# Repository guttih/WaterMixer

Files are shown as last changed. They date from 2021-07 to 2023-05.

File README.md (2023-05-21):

# Water Mixer

This project mixes water temperature from a 1/2" hot water pipe and a 1/2" cold water pipe out to a single 3/4" output 
water pipe.  A electrical valve controls the flow from the hot water pipe and another electrical valve controls the cold
water pipe.  A Temperature sensor is put into the 3/4" output water pipe to sense the current heat of the outgoing water.
Finally the third electrical valve is used to drain the hot tub. 

## Related links

- Project page (todo:)
- [Experiment page]
- [Hot-tub]
- Project [Development documents]

## Parts in project

- 1 x 12V Power supply
- 2 x [DC_STEPDOWN]
- 1 x [ESP32 Development Board]
- 1 x [DS18B20 Digital Temperature Sensor G3/4]
- 1 x [Logic level converter]
- 1 x [Dac MCP4728]
- 3 x [Proportional Valve Brass controllable with 0-5V]
- 1 x [LCD touch display]

## Api

Supported methods, requests and responses are described in the
[API methods]
## Wiring the project

### Schematic

```
                                                                                         +12V
                                                                                          ┬
  ┌───────────────────────────────────────────────────────────────────────────────────────┤
  │ ┌───────────────────┬──────────────────┬────────────────┬───────────────────────┬──┐  │
  │ │                   │                  │  ╔══════════╗  │  ╔═════════════╗      ┴  │  │
  │ │ ╔══════════════╗  │  ╔═════════════╗ │  ║ Pressure ║  │  ║     ADC     ║     GND │  │
  │ │ ║ POWER SOURCE ║  │  ║ DC_STEPDOWN ║ │  ║  Sensor  ║  │  ║   ADS1115   ║         │  │
  │ │ ║              ║  │  ║   -Vo(GND) -╟─┘  ║          ║  │  ║             ║         │  │
  │ │ ║              ║  │  ║   +Vo(+5V) -╟─┐  ║    Black-╟──┴──╢-G           ║         │  │
  │ │ ║              ║  │  ║             ║ │  ║    Green-╟─────╢-A0          ║         │  │
  │ └─╢-     GND    -╟──┴──╢-GND         ║ │  ║          ║     ╢-A1          ║         │  │
  └───╢-    +12V    -╟─────╢-VIN         ║ │  ║          ║     ╢-A2          ║         │  │
      ╚══════════════╝     ╚═════════════╝ │  ║          ║     ╢-A3          ║         │  │
                                           │  ║      Red-╟─┬───╢-V           ║         │  │
                      +5V                  │  ╚══════════╝ │ ┌─╢-CL       DA-╟─┐       │  │
                       ┬  ┌────────────────┴───────────────┘ │ ╚═════════════╝ │       │  │
                       └──┤                                  │                 │       │  │
                          │ ╔═══════════╗                    │ ╔═════════════╗ │       │  │
                          │ ║  -ESP32-  ║  ╔═════════════╗   │ ║     DAC     ║ │       │  │
                          │ ║           ║  ║ Logic Level ║   │ ║   MCP4728   ║ │       │  │
                          │ ║           ║  ║  converter  ║   │ ║             ║ │       │  │
                          └─╢-VIN   G14-╟──╢-LV3     HV3-╟───┴─╢-CL          ║ │       │  │
                            ║       G13-╟──╢-LV4     HV4-╟─────╢-DA───────DA-╟─┘       │  │
 +3V3   ╔═══════════╗       ║           ║  ║             ║     ║             ║         │  │
  ┬     ║  Resistor ║       ║           ║  ║             ║ +5V ║           D-╟──────┐  │  │
┌─┴─────╢-  4.7kΩ  -╟─────┬─╢-G25       ║  ║             ║  ┬  ║           C-╟      │  │  │
│       ╚═══════════╝     │ ║       3V3-╟──╢-LV       HV-╟──┴──╢-V         B-╟────┐ │  │  │
│       ╔═══════════╗     │ ║       GND-╟──╢-GND     GND-╟──┬──╢-G         A-╟──┐ │ │  │  │
│       ║  DS18B20  ║     │ ║           ║  ╚═════════════╝  ┴  ╚═════════════╝  │ │ │  │  │
│       ║   Temp    ║     │ ║           ║                  GND                  │ │ │  │  │
│       ║           ║     │ ║           ║                                       │ │ │  │  │
│       ║    SIGNAL-╟─(YE)┘ ║           ║   ┌───────────────────────────────────┘ │ │  │  │
├──(RD)─╢-VCC       ║       ║           ║   │    ┌────────────────────────────────┘ │  │  │
│ ┌(BL)─╢-GND       ║       ║           ║   │    │    ┌─────────────────────────────┘  │  │
│ │     ╚═══════════╝       ║  -ESP32-  ║   │    │    │        ╔════════════╗          │  │
│ │                         ║           ║   │    │    │        ║   Valve D  ║          │  │
│ │                         ║           ║   │    │    │        ║        GND-╟─(BL)─────┤  │
│ │                         ║           ║   │    │    └───(GR)─╢-LIN    ERR-╟─(YE)─    ┴  │
│ │                         ║           ║   │    │             ║    PWM Out-╟─(WT)─   GND │
│ ├─────────────────────┬───╢-GND       ║   │    │             ║        VCC-╟─(RD)────────┤
│ │  ╔══════════════╗   │   ║           ║   │    │             ╚════════════╝             │
│ │  ║   LCD TOUCH  ║   │   ║           ║   │    │             ╔════════════╗             │
│ │  ║    DISPLAY   ║   │   ║           ║   │    │             ║   Valve C  ║             │
│ │  ║              ║   │   ║           ║   │    │             ║        GND-╟─(BL)─────┐  │
│ │  ║          GND-╟───┘   ║  -ESP32-  ║   │    └─────── (GR)─╢-LIN    ERR-╟─(YE)─    ┴  │
│ │  ║      SD_MOSI-╟─┐     ║           ║   │                  ║    PWM Out-╟─(WT)─   GND │
│ │  ║         MOSI-╟─┼───┐ ║           ║   │                  ║        VCC-╟─(RD)────────┤
│ │  ║        T_DIN-╟─┘   │ ║           ║   │                  ╚════════════╝             │
│ │  ║       SD_SCK-╟─┐   │ ║           ║   │                  ╔════════════╗             │
│ │  ║          SCK-╟─┼─┐ │ ║           ║   │                  ║   Valve H  ║             │
│ │  ║        T_CLK-╟─┘ │ └─╢-G23       ║   │                  ║        GND-╟─(BL)─────┐  │
│ │  ║         T_DO-╟─┐ └───╢-G18       ║   └─────────────(GR)─╢-LIN    ERR-╟─(YE)─    ┴  │
│ │  ║      SD_MISO-╟─┴─────╢-G19       ║                      ║    PWM Out-╟─(WT)─   GND │
│ │  ║           CS-╟───────╢-G15       ║                      ║        VCC-╟─(RD)────────┤
│ │  ║        RESET-╟───────╢-G4        ║                      ╚════════════╝             │
│ │  ║           DC-╟───────╢-G2        ║  ┌─────────────────────────┐                    │
│ │  ║        SD_CS-╟───────╢-G5        ║  │        ╔═════════════╗  │                    │
│ │  ║         T_CS-╟───────╢-G21       ║  │        ║ DC_STEPDOWN ║  │                    │
│ │  ║              ║       ║  -ESP32-  ║  │        ║             ║  │                    │
│ │  ║          VCC-╟─┐     ╚═══════════╝  │  ┌─────╢- -Vo( GND) -╟  │  ┌────┐            │
│ │  ║          LED-╟─┴────────────────────┘  │  ┌──╢- +Vo(+3V3) -╟──┘  │    ┴            │
│ │  ╚══════════════╝                         │  │  ║         GND-╟─────┘   GND           │
│ └───────────────────────────────────────────┘  │  ║         VIN-╟───────────────────────┘
└────────────────────────────────────────────────┘  ╚═════════════╝                         
```
Legend

- <span style="background: black; color: white">(BL) = Black wire (-Ground)</span>
- <span style="background: red; color: white">(RD) = Red wire (+VCC)</span>
- <span style="background: yellow; color: black">(YE) = Yellow wire</span>
- <span style="background: green; color: white">(GR) = Green wire (voltage signal)</span>
- <span style="background: white; color: black">(WT) = White wire</span>
- GND    : Ground.
- ` ┴` 
- `GND`  : Ground.  When there is no room to connect the GND on the drawing, this notation is used.  Note, *all grounds are connected together*.
- VIN    : 5V pin on the esp32 pin.
- G34    : Esp32 GPIO 34 pin which is used to measure voltage coming from pressure sensor.
- G25    : Esp32 GPIO 25 pin which is used to communicate with the temperature sensor.
- G12    : Esp32 GPIO 12 pin which is used control the hot water valve.
- G14    : Esp32 GPIO 14 pin which is used control the cold water valve.
- G32    : Esp32 GPIO 32 pin which is used control the drain water valve.
- G##    : Other esp32 pins used to control the touch display and read and write to a sd card.
- Valve H: Hot valve
- Valve C: Cold valve
- Valve D: Drain valve

## Software development

The software for this project was developed using [PlatformIO].

### Tests

There are two kinds of tests in this project, *integration tests* and *unit tests*.

__Integration tests__:
*integration tests* are located in the `./test` directory.

On windows 10, best would be if you would add this location to your PATH system environment variable __C:\Users\your_user_name\.platformio\penv\Scripts__ to get access to the pio.exe application.
C:\Users\gudjons\.platformio\penv\Scripts
Then you can run the tests with this command `pio test`

[DC_STEPDOWN]:https://www.aliexpress.com/item/32531438467.html?spm=a2g0s.9042311.0.0.27424c4dWJSXmG
[ESP32 Development Board]:https://www.aliexpress.com/item/32801621054.html?spm=a2g0s.9042311.0.0.27424c4dOggB1n
[DS18B20 Digital Temperature Sensor G3/4]:https://www.aliexpress.com/item/32881183992.html?spm=a2g0s.12269583.0.0.43c751fcxDyDbt
[Logic level converter]:https://www.aliexpress.com/item/32308653416.html?spm=a2g0s.9042311.0.0.27424c4dy510IB
[Dac MCP4728]:https://www.aliexpress.com/item/32975252305.html?spm=a2g0s.12269583.0.0.142b3d73bl1KXq
[Proportional Valve Brass controllable with 0-5V]:https://www.aliexpress.com/item/33037988030.html?spm=a2g0s.12269583.0.0.49d04a42eL9zNl
[Experiment page]: https://guttih.com/list/project-hottub-temp
[Hot-tub]:http://192.168.1.79/list/project-hottub
[cmake]:https://cmake.org/download/#latest
[PlatformIO]:https://platformio.org/
[Development documents]: docs/development/development.md
[LCD touch display]: https://www.aliexpress.com/item/4000030399357.html?spm=a2g0s.12269583.0.0.687d6973QvjfAl
[API methods]: docs/apiMethods.adoc

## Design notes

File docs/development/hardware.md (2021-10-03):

# Hardware
This document describes each device, what voltage it uses and where it was bought.

## esp32
__Esp32 Development board__

This device handles all the work and is connected to all other devices.

 - Bought [here](https://www.aliexpress.com/item/32801621054.html?spm=a2g0s.9042311.0.0.27424c4dOggB1n)
 - Inventory [Here](http://parts.guttih.com/parts/view/5bfab5e0ec065a5ac2786934)

## temperature_sensor
__DS18B20 3/4" temperature sensor__ 

The sensor provides information on the water pressure in the pipe connected to the hot tub.  
It can run on both 5V and 3.3V power.

- Bought [DS18B20 Color L30mm Thread Specification 3/4"](https://www.aliexpress.com/item/32881183992.html?spm=a2g0s.12269583.0.0.43c751fcxDyDbt) 
- Inventory [Here](http://parts.guttih.com/parts/view/60c1c1c063ec3e056918c551)

## LLC 
__Logic level converter__

This device is used to convert 3.3V logic signals from the esp32 to 5V logic signals for the DAC.

- Bought [here](https://www.aliexpress.com/item/Free-shipping-4-channel-IIC-I2C-Logic-Level-Converter-Bi-Directional-Module-5V-to-3-3V/32308653416.html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)
- Inventory [Here](http://parts.guttih.com/parts/view/5bf9e9d1a66f3c7ee749efc5)

## MCP4728 
__DAC MCP4728 Module__

This device is used to send voltage ranging from 0-5 volts which a proportional
valve understands.

- Bought [here](https://www.aliexpress.com/item/32975252305.html?spm=a2g0s.12269583.0.0.142b3d73bl1KXq)
- Inventory [Here](http://parts.guttih.com/parts/view/61110ca1643bf7053b856df2)

## proportional_valve
__12V Proportional Valve__

There are three valves in this project, one 3/8" and two 3/4" valves.  They work exactly the same so we will consider 
them all three units of the same device.  The 3/8" unit will be controlling the drain water flow.

- Bought 2 x [Voltage: DC9V to DC24V, Specification: DN20 BSP Thread, Wiring Control: 0V to 5V Signal](https://www.aliexpress.com/item/32819881011.html?spm=a2g0s.12269583.0.0.112c1eaeyGDt8f)
- Bought 1 x [Voltage:DC9V-24V 0-5V, Specification: DN10 Brass Valve, Thread Type: NPT](https://www.aliexpress.com/item/33037988030.html?spm=a2g0s.12269583.0.0.6c674a42N25diC)
- Inventory [Here](http://parts.guttih.com/parts/view/5e2589736d7d870510d99be2)

## lcd_touch_display
  __3.2 Display module with touch and SD card reader__

  The device __needs 3.3V__ power to work.  The J1 has been soldered so 5V is out of the question.

- Bought [here](https://www.aliexpress.com/item/33040270372.html?spm=a2g0s.12269583.0.0.437c3e40dV19J4)
- Inventory [Here](http://parts.guttih.com/parts/view/60f1a0d4ea0ad5055e96116e)

## 12v_power_supply

Needed to power the three _12V Proportional Valves_

__Not selected yet__
- Bought todo: select product
- Inventory todo: add product to inventory

## 5v_power_supply

__DC_STEPDOWN__ 

This small adjustable step down power supply is needed to supply the pressure sensor and the Esp32 with power.
This unit will get power from the __12v_power_supply__ and will be be adjusted to give __5.05V__ output power.

- Bought [DC_STEPDOWN](https://www.aliexpress.com/item/32531438467.html?spm=a2g0s.9042311.0.0.27424c4dWJSXmG)
- Inventory [Here](http://192.168.1.79:6300/parts/view/5bfae6c1ec065a5ac278698f)

## 3v3_power_supply

__DC_STEPDOWN__ 

This small adjustable step down power supply is needed to supply the temperature sensor and the lcd touch display with power.
This unit will get power from the __12v_power_supply__ and will be be adjusted to give __3.2V__ output power.

- Bought [DC_STEPDOWN](https://www.aliexpress.com/item/32531438467.html?spm=a2g0s.9042311.0.0.27424c4dWJSXmG)
- Inventory [Here](http://192.168.1.79:6300/parts/view/5bfae6c1ec065a5ac278698f)

## pressure_sensor

This sensor needs 5V power to work and provides information on the water pressure in the pipe connected to the hot tub.

- Bought ~~[Pressure Sensor 5V 1/8" 5 Psi](https://www.aliexpress.com/item/4000263209249.html?spm=a2g0s.12269583.0.0.5dd91d80iwCJ6y)~~ which is incorrect because it woks on 0-0.345 bars
- Should have bought [Pressure Sensor 5V 1/8" 60 Psi](https://www.aliexpress.com/item/4000263209249.html?spm=a2g0s.12269583.0.0.5dd91d80iwCJ6y) which works on 0-4 bars.
- Inventory [Here](http://parts.guttih.com/parts/view/60cc6e7b395390058cb396d8)

 ### Related pages
 * [Readme]
 * [Product requirements]
 * [System requirements]
 * [Product requirements]
 * [User stories]
 * [Hardware]
 * [Releases]

[Readme]: ../../README.md
[Product requirements]: ./productRequirements.md
[System requirements]: ./systemRequirements.md
[User stories]: ./userStories.md
[Hardware]: ./hardware.md
[Releases]: ./releases.md

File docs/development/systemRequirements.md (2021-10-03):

# System Requirements
This document (SRD) provides information about what environment and hardware will be needed to make this product work.

## Hardware requirements

In general to make this product work these hardware modules will be needed.

Table column description:
  * __Hardware Id__ A short, unique, one word name of the hardware or device in question.
  * __Name__ Name of the part.
  * __Units__ How many peases of this kind of part is needed.
  * __R__ For what release is this parted needed.  Read about [Releases].

|  Hardware Id | Name | Units | R | The device is needed because |
|:---:|---|:---:|---|---|
| [esp32] | ESP32 Development Board | 1 | [0.5] | Control everything |
| [temperature_sensor] | DS18B20 3/4" temperature sensor | 2 | [0.5] | Provide water temperature in the outgoing pipe |
| [LLC] | Logic level converter - 4 channels | 1 | [0.5] | To allow esp32 to control DAC on 5V |
| [MCP4728] | Digital to analog converter (DAC) | 1 | [0.5] | Allow esp32 to control the valves |
| [proportional_valve] | Proportional Valve Brass controllable with 0-5V | 3 | [0.5] | To control the water flow in the pipes |
| [lcd_touch_display]  | 2.8" LCD Touch Display | 1 | [0.5] | To pass user information and get input from user |
| [12v_power_supply] | 12 volt power supply | 1 | [0.5] | Power the three [proportional_valve] |
| [5v_power_supply] | 5 volt power supply | 1 | [0.5] | Power [esp32], [temperature_sensor] and [pressure_sensor] |
| [3v3_power_supply] | 3.3 volt power supply | 1 | [0.5] | Power [lcd_touch_display] |
| [pressure_sensor] | 60 psi pressure sensor | 1 | [0.5] | Needed to test the water level of the hot tub |

## The Plumbing

This diagram shows the general idea, on where the electric valves and sensors should be located in the water pipe system.
Overview image of the whole system

 ### Related pages
 * [Readme]
 * [Product requirements]
 * [System requirements]
 * [Product requirements]
 * [User stories]
 * [Hardware]
 * [Releases]

[Readme]: ../../README.md
[Product requirements]: ./productRequirements.md
[System requirements]: ./systemRequirements.md
[User stories]: ./userStories.md
[Hardware]: ./hardware.md
[Releases]: ./releases.md

[0.5]: ./releases.md#release-05---bare-minimum
[0.6]: ./releases.md#release-06--hardware-installed
[0.7]: ./releases.md#release-07---additional-features
[0.8]: ./releases.md#release-08---remote-access
[0.9]: ./releases.md#release-09---boxed
[1.0]: ./releases.md#release-10
[1.1]: ./releases.md#release-11

[esp32]: ./hardware.md#esp32
[temperature_sensor]: ./hardware.md#temperature_sensor
[LLC]: ./hardware.md#LLC
[MCP4728]: ./hardware.md#MCP4728
[proportional_valve]: ./hardware.md#proportional_valve
[lcd_touch_display]: ./hardware.md#lcd_touch_display
[12v_power_supply]: ./hardware.md#12v_power_supply
[5v_power_supply]: ./hardware.md#5v_power_supply
[3v3_power_supply]: ./hardware.md#3v3_power_supply
[pressure_sensor]: ./hardware.md#pressure_sensor

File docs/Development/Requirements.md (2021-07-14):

# Product requirements
This Product Requirements Document(PRD) describes the requirements the Water mixer project needs to fulfill.  In this 
document, the Water mixer project and all its components will be referred to as the unit.

## Purpose
The main purpose of this project is to provide a user with an easy way to control water flow to and from a hot tub.  
A user should be able to command the unit to fill a hot tub at a specific temperature.  The user should be able to use 
it to control how fast the water flows to the hot tub and also to drain the hot tub.

To achieve this the unit will need to provide the user with information about it’s status and a way to give it commands.
  The user should be able to get the status and and give commands in two ways:

  * __At premises__ When the user is standing in front of the device he should be able to see it’s status, that is, 
  view the value of any status variable and to be able to give any of the available commands.

  * __Remotely__   When the user is not standing in front of the unit, he should be able to see it’s status, that is, 
  view the value of any status variable and to be able to give any of the available commands.

## Features
To be able to fulfill the purpose of this product the features will need to be described and implemented before release.  
They need to be prioritized and later selected into releases.  High priority features will be released first, 
and other lower priority features will be selected and released later.

### Users
Description of the two main personas this product is intended for.
 
   * __John__ is a 30 years old DIY kind a guy.  John knows a little programming, knows about GitHub and knows 
   JavaScript.  He understands the concept of a API and what a PID controller does, but is no specialist.

   * __Kamila__ is a non 11 years old non technical kind a girl.  She knows how to use a computer and a phone and 
   knows how to use a web browser.

Table column description:
  * __Feature Id__ Short one word name of feature
  * __User Story__ As a [persona], I [want to], [so that]
  * __P__ Priority/Importance of the feature. Available values: `H` `N` `L`. Where H=High, N=Normal and L = Low.
  * __R__ Feature is selected into a release numbered something. Read about [Releases].
  * __Notes__ Additional considerations or better explanation of the story.

|  Feature Id | User Story | P | R | Notes |
|:---:|---|---|---|---|
| LCD_FILL | As Kamila, I stand in front of the unit and want to fill the hot tub | H | [0.5] | |
| LCD_STOP | As Kamila, I stand in front of the unit and want to stop the flow to the hot tub | H | [0.5] | |
| LCD_DRAIN | As Kamila, I stand in front of the unit and want to drain the hot tub | H | [0.5] | |
| LCD_STATUS_TEMP | As Kamila, I stand in front of the unit and want to know the water temperature | N | [0.5] | |
| LCD_TEMP | As Kamila, I stand in front of the unit and want to change the water temperature flowing to the hot tub | H | [0.5] | |
| LCD_STATUS_FLOW | As Kamila, I stand in front of the unit and want to know the water flow rate | N | [0.7] | |
| LCD_FLOW_SLOW | As Kamila, I stand in front of the unit and want to make water flow slowly to the hot tub | N | [0.7] | |
| LCD_STATUS_WHEN_FULL | As Kamila, I stand in front of the unit and want to know when the hot tub will be full | L | [1.0] |  This is after some one has initiated the fylling process |
| LCD_STATUS_WHEN_EMPTY  | As Kamila, I stand in front of the unit and want to know when the hot tub will be fully drained | L | [1.0] |  This is after some one has initiated the draining process |
| LCD_STATUS_WATER_LEVEL | As Kamila, I stand in front of the unit and want to know the current hot tub water level | L | [1.0] | |

[Releases] :./Releases.md
[VoffCon] :http://voffcon.com/

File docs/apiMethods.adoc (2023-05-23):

:title-page:
:doctitle: API methods v{doc-version}: {system-name} v{version}
:author: Guðjón Hólm Sigurðsson
:header-text: {system-name} API methods
:version: 1.0
:doc-version: 1.0
:date:  2023 Mai 21
:doctype: book
:encoding: utf-8
:lang: en
:toc: left
:toc-title: Table of Contents
:toclevels: 2
:numbered:
:experimental:
:xrefstyle: short
:source-highlighter: CodeRay
:source-highlighter: highlight.js
:imagesdir: images
:chapter-signifier:
:system-name: WaterMixer
:stylesdir: ./styles
:stylesheet: style.css

= {doctitle}

This document describes the API methods supported by the {system-name}.  
Ones you know the ip number of the device these methods can be appended to the
device path.  The device will respond to port 80.

== Getting started

.Test access to the device

Let's say that a {system-name} device has been assigned the ip address *192.168.1.28* and 
we want to test if it's up and running.  You could do one of the following:
 
 - Paste this path to a web browser _http://192.168.1.28/started_
 - Give command: `curl http://192.168.1.28/started`
 - Give command: `wget -q -S -O - http://192.168.1.28/started`
 
In all three cases the response should be the following json object, (with different numbers of course) containing information about when the device was started.

[source,json]
----
{"date":{"year":2023,"month":5,"day":21,"hours":17,"minutes":46,"seconds":10}}
----

If you see this response, you have access to the device and it is working as it should.

.Posting with curl

If you need to post to the device you could use curl to do that.  Here is an example on how
to make the device fill the hot tub with temperature 37.

[source,shell]
----
 curl -X POST http://192.168.1.28/custom  -H "Content-Type: application/json" -d '{"cmd":"fill","temperature":37}'
----

== Methods overview

The device support the following http methods.

.Methods
[cols="1,1,3,2,1"]
|===
| *Method*  | *Resource*        | *Description*                                              | *Details*                          | *Type*
|   GET     |  `/pinout`        | Name and number of the connected virtual pins.             | <<Get /pinout response>>           |  Json 
|   GET     |  `/started`       | When was the device started.                               | <<Get /started response>>          |  Json 
|   GET     |  `/pins`          | Information about device pins, like pin name, pin number, 
                                  pin value and pin type.                                    | <<Get /pins response>>             |  Json 
|   POST    |  `/pins`          | Set new pin values to pins.                                | <<Post /pins request>>            |  Json 
|   GET     |  `/status`        | Status of the device, This object contains values for pins, 
                                  whitelist, macAddress, deviceId, hostName and mixer values.| <<Get /status response>>           |  Json 
|   GET     |  `/samples`       | Values recorded by system scan returned as a json object.  | <<Get /samples response>>          |  Json 
|   GET     |  `/samples/csv`   | Values recorded by system scan returned as a csv document, 
                                  where fields are separated by semicolon.                   | <<Get /samples/csv response>>      |  Csv 
|   GET     |  `/samples/csv/,` | Values recorded by system scan returned as a csv document, 
                                  where fields are separated by comma.                       | xref:Get /samples/csv/, response[] |  Csv
|   GET     |  `/monitors`      | Get pin monitors.                                          | <<Get /monitors response>>         |  JsonArray 
|   POST    |  `/monitors`      | Add a pin monitor.                                         | <<Post /monitors request>>         |  Json
|   DELETE  |  `/monitors`      | Delete pin monitors.                                       | <<Delete /monitors request>>       |  JsonArray
|   POST    |  `/whitelist`     | Add a ip address to whitelist.                             | <<Post /whitelist request>>        |  Json 
|   DELETE  |  `/whitelist`     | Delete a ip address from whitelist.                        | <<Delete /whitelist request>>      |  Json 
|   POST    |  `/custom`        | Send commands to fill, stop, drain and change temperature 
                                  of the hot tub.                                            | <<Post /custom request>>          |  Json 
|===

== API Resources

More detailed information about the http requests.  

Note that the json object examples shall not have any extra spaces or end lines, but I 
will format the json object examples a little, for illustrative purposes in this document.

=== Resource /pinout

Returns name and number of the connected virtual pins.

===== Get /pinout response

[source, json]
----
{
    "valveHot":50,
    "valveCold":51,
    "valveDrain":52,
    "pressure":53,
    "temperature":54,
    "desiredTemperature":55
}
----

=== Resource /started

Date when the device was turned on.

===== Get /started response

[source, json]
----
{
    "date": {
        "year": 2023,
        "month": 5,
        "day": 21,
        "hours": 17,
        "minutes": 46,
        "seconds": 10
    }
}
----

=== Resource /pins

Information about device pins, like pin name, pin number, pin value and pin type.

===== Get /pins response

[source, json]
----
{
    "type": 2, 
    "pins":[ {"pin":50,"val":0,  "m":4,"name":"valveHot"},
             {"pin":51,"val":0,  "m":4,"name":"valveCold"},
             {"pin":52,"val":0,  "m":4,"name":"valveDrain"},
             {"pin":53,"val":90, "m":4,"name":"pressure"},
             {"pin":54,"val":230,"m":4,"name":"temperature"},
             {"pin":55,"val":369,"m":4,"name":"desiredTemperature"}
           ]
}
----

===== Post /pins request

Change pin value, in this case pin number 55 will get the value 378.

[source, json]
----
{
    "55": 378
}
----

===== Post /pins response

Current status of all pins after the change is done.

[source, json]
----
{
    "type": 2,
    "pins": [ { "pin": 50,"val": 0,  "m": 4,"name":"valveHot"},
              { "pin": 51,"val": 0,  "m": 4,"name":"valveCold"},
              { "pin": 52,"val": 0,  "m": 4,"name":"valveDrain"},
              { "pin": 53,"val": 80, "m": 4,"name":"pressure"},
              { "pin": 54,"val": 237,"m": 4,"name":"temperature"},
              { "pin": 55,"val": 378,"m": 4,"name":"desiredTemperature"}
    ]
}
----

=== Resource /status

Status of the device, This object contains values for pins, 
whitelist, macAddress, deviceId, hostName and mixer values.

===== Get /status response

[source, json]
----
{
    "type": 7,
    "pins":[ {"pin":50,"val":0,"m":4,"name":"valveHot"},
             {"pin":51,"val":0,"m":4,"name":"valveCold"},
             {"pin":52,"val":0,"m":4,"name":"valveDrain"},
             {"pin":53,"val":90,"m":4,"name":"pressure"},
             {"pin":54,"val":230,"m":4,"name":"temperature"},
             {"pin":55,"val":369,"m":4,"name":"desiredTemperature"}
           ],
    "whitelist": ["192.168.1.79", "192.168.1.198"],
    "macAddress": "F0:08:D1:C8:39:34",
    "deviceId": "61052c38bc1fdd0526aedf31",
    "hostName": "watermixer",
    "ip": "192.168.1.28",
    "port": 80,
    "date": { "year": 2023,"month": 5,   "day": 21,
              "hours": 17, "minutes": 46,"seconds": 10},
    "mixer": {
        "hotValveFlow": 0.00,
        "coldValveFlow": 0.00,
        "drainValveFlow": 0.00,
        "currentTemperature": 22.50,
        "desiredTemperature": 36.00,
        "currentPressure": 0.44,
        "mode": 1
    }
}
----

=== Resource /samples

Values recorded by system scan returned as a json object.

===== Get /samples response

[source, json]
----
{
    "type":9,
    "samples":[
        {"hot":0.00, "cold":100.00, "pressure":2.14, "temperature":12.31, "time":44169521},
        {"hot":0.49, "cold":100.00, "pressure":2.15, "temperature":11.38, "time":44229735},
        {"hot":0.98, "cold":100.00, "pressure":2.15, "temperature":10.50, "time":44289813},
        {"hot":1.47, "cold":100.00, "pressure":2.16, "temperature":9.81, "time":44350037},
        {"hot":1.95, "cold":100.00, "pressure":2.13, "temperature":9.31, "time":44410125},
        {"hot":2.44, "cold":100.00, "pressure":2.15, "temperature":8.88, "time":44470206},
        {"hot":2.93, "cold":100.00, "pressure":2.14, "temperature":8.50, "time":44530235},
        {"hot":3.42, "cold":100.00, "pressure":2.14, "temperature":8.19, "time":44590393},
        {"hot":3.91, "cold":100.00, "pressure":2.14, "temperature":8.13, "time":44650538},
        {"hot":4.40, "cold":100.00, "pressure":2.15, "temperature":8.00, "time":44710627},
        {"hot":4.88, "cold":100.00, "pressure":2.12, "temperature":7.94, "time":44770663},
        {"hot":5.37, "cold":100.00, "pressure":2.12, "temperature":7.87, "time":44830860},
        {"hot":5.86, "cold":100.00, "pressure":2.07, "temperature":7.81, "time":44891024},
        {"hot":6.35, "cold":100.00, "pressure":2.11, "temperature":7.75, "time":44951211},
        {"hot":6.84, "cold":100.00, "pressure":2.13, "temperature":7.75, "time":45011381},
        {"hot":7.33, "cold":100.00, "pressure":2.12, "temperature":7.69, "time":45071485},
        {"hot":7.81, "cold":100.00, "pressure":2.13, "temperature":7.69, "time":45131637},
        {"hot":8.30, "cold":100.00, "pressure":2.13, "temperature":7.69, "time":45191842},
        {"hot":8.79, "cold":100.00, "pressure":2.05, "temperature":7.69, "time":45251952},
        {"hot":9.28, "cold":100.00, "pressure":2.26, "temperature":7.62, "time":45312028},
        {"hot":9.77, "cold":100.00, "pressure":2.22, "temperature":7.62, "time":45372239},
        {"hot":10.26, "cold":100.00, "pressure":2.22, "temperature":7.69, "time":45432398},
        {"hot":10.74, "cold":100.00, "pressure":2.23, "temperature":7.69, "time":45492571},
        {"hot":11.23, "cold":100.00, "pressure":2.20, "temperature":7.69, "time":45552738},
        {"hot":11.72, "cold":100.00, "pressure":2.23, "temperature":9.25, "time":45612956},
        {"hot":12.21, "cold":100.00, "pressure":2.24, "temperature":9.69, "time":45673176},
        {"hot":12.70, "cold":100.00, "pressure":2.25, "temperature":10.63, "time":45733374},
        {"hot":13.19, "cold":100.00, "pressure":2.26, "temperature":10.81, "time":45793585},
        {"hot":13.68, "cold":100.00, "pressure":2.35, "temperature":14.44, "time":45853801},
        {"hot":14.16, "cold":100.00, "pressure":2.34, "temperature":14.69, "time":45913934},
        {"hot":14.65, "cold":100.00, "pressure":2.39, "temperature":17.50, "time":45974149},
        {"hot":15.14, "cold":100.00, "pressure":2.40, "temperature":17.75, "time":46034242},
        {"hot":15.63, "cold":100.00, "pressure":2.48, "temperature":21.94, "time":46094450},
        {"hot":16.12, "cold":100.00, "pressure":2.54, "temperature":23.87, "time":46154665},
        {"hot":16.61, "cold":100.00, "pressure":2.52, "temperature":23.94, "time":46214686},
        {"hot":17.09, "cold":100.00, "pressure":2.56, "temperature":26.00, "time":46274796},
        {"hot":17.58, "cold":100.00, "pressure":2.53, "temperature":26.50, "time":46334934},
        {"hot":18.07, "cold":100.00, "pressure":2.65, "temperature":30.37, "time":46395153},
        {"hot":18.56, "cold":100.00, "pressure":2.68, "temperature":30.75, "time":46455238},
        {"hot":19.05, "cold":100.00, "pressure":2.68, "temperature":31.12, "time":46515380},
        {"hot":19.54, "cold":100.00, "pressure":2.74, "temperature":33.75, "time":46575430},
        {"hot":20.02, "cold":100.00, "pressure":2.74, "temperature":33.50, "time":46635497},
        {"hot":20.51, "cold":100.00, "pressure":2.77, "temperature":36.75, "time":46695622},
        {"hot":21.00, "cold":100.00, "pressure":2.80, "temperature":37.06, "time":46755713},
        {"hot":21.49, "cold":100.00, "pressure":2.85, "temperature":39.19, "time":46815942},
        {"hot":21.98, "cold":100.00, "pressure":2.84, "temperature":39.25, "time":46876112},
        {"hot":22.47, "cold":100.00, "pressure":2.89, "temperature":41.25, "time":46936147},
        {"hot":22.95, "cold":100.00, "pressure":2.89, "temperature":40.44, "time":46996375},
        {"hot":23.44, "cold":100.00, "pressure":2.92, "temperature":43.31, "time":47056583},
        {"hot":23.93, "cold":100.00, "pressure":2.94, "temperature":43.25, "time":47116748},
        {"hot":24.42, "cold":100.00, "pressure":2.98, "temperature":44.19, "time":47176968},
        {"hot":24.91, "cold":100.00, "pressure":2.97, "temperature":45.00, "time":47237054},
        {"hot":25.40, "cold":100.00, "pressure":3.04, "temperature":48.00, "time":47297150},
        {"hot":25.89, "cold":100.00, "pressure":3.04, "temperature":48.38, "time":47357358},
        {"hot":26.37, "cold":100.00, "pressure":3.03, "temperature":48.38, "time":47417520},
        {"hot":26.86, "cold":100.00, "pressure":3.08, "temperature":50.19, "time":47477706},
        {"hot":27.35, "cold":100.00, "pressure":3.07, "temperature":50.06, "time":47537900},
        {"hot":27.84, "cold":100.00, "pressure":3.08, "temperature":50.50, "time":47597946},
        {"hot":28.33, "cold":100.00, "pressure":3.15, "temperature":53.19, "time":47658043},
        {"hot":28.82, "cold":100.00, "pressure":3.14, "temperature":53.63, "time":47718150},
        {"hot":29.30, "cold":100.00, "pressure":3.15, "temperature":53.81, "time":47778176},
        {"hot":29.79, "cold":100.00, "pressure":3.16, "temperature":55.44, "time":47838221},
        {"hot":30.28, "cold":100.00, "pressure":3.17, "temperature":55.50, "time":47898417},
        {"hot":30.77, "cold":100.00, "pressure":3.19, "temperature":55.56, "time":47958561},
        {"hot":31.26, "cold":100.00, "pressure":3.18, "temperature":55.81, "time":48018660},
        {"hot":31.75, "cold":100.00, "pressure":3.21, "temperature":57.00, "time":48078697},
        {"hot":32.23, "cold":100.00, "pressure":3.23, "temperature":57.56, "time":48138758},
        {"hot":32.72, "cold":100.00, "pressure":3.28, "temperature":58.00, "time":48198818},
        {"hot":33.21, "cold":100.00, "pressure":3.24, "temperature":58.44, "time":48258832},
        {"hot":33.70, "cold":100.00, "pressure":3.26, "temperature":59.56, "time":48318940},
        {"hot":34.19, "cold":100.00, "pressure":3.27, "temperature":59.81, "time":48378958},
        {"hot":34.68, "cold":100.00, "pressure":3.27, "temperature":60.38, "time":48439012},
        {"hot":35.16, "cold":100.00, "pressure":3.29, "temperature":60.44, "time":48499093},
        {"hot":35.65, "cold":100.00, "pressure":3.26, "temperature":60.88, "time":48559212},
        {"hot":36.14, "cold":100.00, "pressure":3.29, "temperature":54.81, "time":48619245},
        {"hot":36.63, "cold":100.00, "pressure":3.29, "temperature":61.44, "time":48679327},
        {"hot":37.12, "cold":100.00, "pressure":3.29, "temperature":62.50, "time":48739388},
        {"hot":37.61, "cold":100.00, "pressure":3.30, "temperature":62.38, "time":48799645},
        {"hot":38.10, "cold":100.00, "pressure":3.26, "temperature":62.88, "time":48859707},
        {"hot":38.58, "cold":100.00, "pressure":3.36, "temperature":64.06, "time":48919948},
        {"hot":39.07, "cold":100.00, "pressure":3.32, "temperature":65.12, "time":48980123},
        {"hot":39.56, "cold":100.00, "pressure":3.35, "temperature":66.44, "time":49040317},
        {"hot":40.05, "cold":100.00, "pressure":3.37, "temperature":67.06, "time":49100410},
        {"hot":40.54, "cold":100.00, "pressure":3.36, "temperature":67.50, "time":49160479},
        {"hot":41.03, "cold":100.00, "pressure":3.36, "temperature":67.56, "time":49220598},
        {"hot":41.51, "cold":100.00, "pressure":3.38, "temperature":68.44, "time":49280707},
        {"hot":42.00, "cold":100.00, "pressure":3.36, "temperature":68.69, "time":49340787},
        {"hot":42.49, "cold":100.00, "pressure":3.39, "temperature":68.31, "time":49400960},
        {"hot":42.98, "cold":100.00, "pressure":3.37, "temperature":68.37, "time":49461121},
        {"hot":43.47, "cold":100.00, "pressure":3.38, "temperature":67.44, "time":49521158},
        {"hot":43.96, "cold":100.00, "pressure":3.38, "temperature":68.19, "time":49581216},
        {"hot":44.44, "cold":100.00, "pressure":3.38, "temperature":68.31, "time":49641237},
        {"hot":44.93, "cold":100.00, "pressure":3.35, "temperature":68.00, "time":49701302},
        {"hot":45.42, "cold":100.00, "pressure":3.35, "temperature":67.44, "time":49761331},
        {"hot":45.91, "cold":100.00, "pressure":3.38, "temperature":67.44, "time":49821438},
        {"hot":46.40, "cold":100.00, "pressure":3.40, "temperature":67.50, "time":49881534},
        {"hot":46.89, "cold":100.00, "pressure":3.40, "temperature":68.37, "time":49941605},
        {"hot":47.37, "cold":100.00, "pressure":3.39, "temperature":68.75, "time":50001742},
        {"hot":47.86, "cold":100.00, "pressure":3.40, "temperature":69.56, "time":50061894},
        {"hot":48.35, "cold":100.00, "pressure":3.42, "temperature":70.44, "time":50122008},
        {"hot":48.84, "cold":100.00, "pressure":3.40, "temperature":70.56, "time":50182077},
        {"hot":49.33, "cold":100.00, "pressure":3.41, "temperature":71.06, "time":50242309},
        {"hot":49.82, "cold":100.00, "pressure":3.41, "temperature":70.25, "time":50302324},
        {"hot":50.31, "cold":100.00, "pressure":3.43, "temperature":70.75, "time":50362351},
        {"hot":50.79, "cold":100.00, "pressure":3.42, "temperature":70.19, "time":50422569},
        {"hot":51.28, "cold":100.00, "pressure":3.45, "temperature":70.69, "time":50482695},
        {"hot":51.77, "cold":100.00, "pressure":3.41, "temperature":70.69, "time":50542739},
        {"hot":52.26, "cold":100.00, "pressure":3.28, "temperature":78.00, "time":50602886},
        {"hot":52.75, "cold":100.00, "pressure":3.29, "temperature":76.50, "time":50663085},
        {"hot":53.24, "cold":100.00, "pressure":3.33, "temperature":74.31, "time":50723256},
        {"hot":53.72, "cold":100.00, "pressure":3.34, "temperature":75.25, "time":50783416},
        {"hot":54.21, "cold":100.00, "pressure":3.32, "temperature":74.31, "time":50843632},
        {"hot":54.70, "cold":100.00, "pressure":3.33, "temperature":75.62, "time":50903692},
        {"hot":55.19, "cold":100.00, "pressure":3.35, "temperature":75.87, "time":50963888},
        {"hot":55.68, "cold":100.00, "pressure":3.35, "temperature":76.75, "time":51024111},
        {"hot":56.17, "cold":100.00, "pressure":3.36, "temperature":75.44, "time":51084350},
        {"hot":56.65, "cold":100.00, "pressure":3.34, "temperature":75.81, "time":51144371},
        {"hot":57.14, "cold":100.00, "pressure":3.31, "temperature":75.94, "time":51204399},
        {"hot":57.63, "cold":100.00, "pressure":3.29, "temperature":76.00, "time":51264560},
        {"hot":58.12, "cold":100.00, "pressure":3.35, "temperature":77.56, "time":51324628},
        {"hot":58.61, "cold":100.00, "pressure":3.33, "temperature":78.00, "time":51384757},
        {"hot":59.10, "cold":100.00, "pressure":3.33, "temperature":77.87, "time":51444928},
        {"hot":59.58, "cold":100.00, "pressure":3.34, "temperature":77.81, "time":51505039},
        {"hot":60.07, "cold":100.00, "pressure":3.31, "temperature":77.31, "time":51565145},
        {"hot":60.56, "cold":100.00, "pressure":3.33, "temperature":77.31, "time":51625357},
        {"hot":61.05, "cold":100.00, "pressure":3.32, "temperature":77.87, "time":51685489},
        {"hot":61.54, "cold":100.00, "pressure":3.35, "temperature":79.06, "time":51745608},
        {"hot":62.03, "cold":100.00, "pressure":3.38, "temperature":79.56, "time":51805779},
        {"hot":62.52, "cold":100.00, "pressure":3.39, "temperature":79.62, "time":51865804},
        {"hot":63.00, "cold":100.00, "pressure":3.38, "temperature":79.56, "time":51925948},
        {"hot":63.49, "cold":100.00, "pressure":3.34, "temperature":79.56, "time":51986087},
        {"hot":63.98, "cold":100.00, "pressure":3.34, "temperature":79.44, "time":52046108},
        {"hot":64.47, "cold":100.00, "pressure":3.30, "temperature":79.50, "time":52106282},
        {"hot":64.96, "cold":100.00, "pressure":3.34, "temperature":78.75, "time":52166358},
        {"hot":65.45, "cold":100.00, "pressure":3.30, "temperature":78.44, "time":52226394},
        {"hot":65.93, "cold":100.00, "pressure":3.31, "temperature":78.37, "time":52286409},
        {"hot":66.42, "cold":100.00, "pressure":3.32, "temperature":76.69, "time":52346450},
        {"hot":66.91, "cold":100.00, "pressure":3.34, "temperature":77.94, "time":52406697},
        {"hot":67.40, "cold":100.00, "pressure":3.36, "temperature":79.31, "time":52466777},
        {"hot":67.89, "cold":100.00, "pressure":3.37, "temperature":79.12, "time":52526843},
        {"hot":68.38, "cold":100.00, "pressure":3.33, "temperature":79.56, "time":52586997},
        {"hot":68.86, "cold":100.00, "pressure":3.32, "temperature":79.37, "time":52647018},
        {"hot":69.35, "cold":100.00, "pressure":3.30, "temperature":78.12, "time":52707058},
        {"hot":69.84, "cold":100.00, "pressure":3.31, "temperature":77.62, "time":52767158},
        {"hot":70.33, "cold":100.00, "pressure":3.34, "temperature":79.06, "time":52827214},
        {"hot":70.82, "cold":100.00, "pressure":3.34, "temperature":79.62, "time":52887387},
        {"hot":71.31, "cold":100.00, "pressure":3.34, "temperature":79.25, "time":52947492},
        {"hot":71.79, "cold":100.00, "pressure":3.35, "temperature":79.69, "time":53007723},
        {"hot":72.28, "cold":100.00, "pressure":3.37, "temperature":79.87, "time":53067869},
        {"hot":72.77, "cold":100.00, "pressure":3.34, "temperature":79.81, "time":53127884},
        {"hot":73.26, "cold":100.00, "pressure":3.31, "temperature":79.75, "time":53188091},
        {"hot":73.75, "cold":100.00, "pressure":3.33, "temperature":78.06, "time":53248223},
        {"hot":74.24, "cold":100.00, "pressure":3.34, "temperature":78.87, "time":53308369},
        {"hot":74.73, "cold":100.00, "pressure":3.36, "temperature":79.31, "time":53368458},
        {"hot":75.21, "cold":100.00, "pressure":3.34, "temperature":79.62, "time":53428686},
        {"hot":75.70, "cold":100.00, "pressure":3.36, "temperature":79.81, "time":53488838},
        {"hot":76.19, "cold":100.00, "pressure":3.39, "temperature":79.87, "time":53548916},
        {"hot":76.68, "cold":100.00, "pressure":3.37, "temperature":79.94, "time":53609094},
        {"hot":77.17, "cold":100.00, "pressure":3.37, "temperature":79.87, "time":53669341},
        {"hot":77.66, "cold":100.00, "pressure":3.38, "temperature":79.94, "time":53729574},
        {"hot":78.14, "cold":100.00, "pressure":3.44, "temperature":79.94, "time":53789615},
        {"hot":78.63, "cold":100.00, "pressure":3.45, "temperature":79.94, "time":53849789},
        {"hot":79.12, "cold":100.00, "pressure":3.43, "temperature":79.94, "time":53909970},
        {"hot":79.61, "cold":100.00, "pressure":3.39, "temperature":79.94, "time":53970191},
        {"hot":80.10, "cold":100.00, "pressure":3.38, "temperature":79.94, "time":54030363},
        {"hot":80.59, "cold":100.00, "pressure":3.40, "temperature":79.94, "time":54090610},
        {"hot":81.07, "cold":100.00, "pressure":3.36, "temperature":79.87, "time":54150839},
        {"hot":81.56, "cold":100.00, "pressure":3.31, "temperature":78.69, "time":54210989},
        {"hot":82.05, "cold":100.00, "pressure":3.33, "temperature":79.44, "time":54271073},
        {"hot":82.54, "cold":100.00, "pressure":3.35, "temperature":79.62, "time":54331154},
        {"hot":83.03, "cold":100.00, "pressure":3.37, "temperature":79.87, "time":54391395},
        {"hot":83.52, "cold":100.00, "pressure":3.34, "temperature":79.87, "time":54451409},
        {"hot":84.00, "cold":100.00, "pressure":3.34, "temperature":79.44, "time":54511536},
        {"hot":84.49, "cold":100.00, "pressure":3.36, "temperature":79.87, "time":54571655},
        {"hot":84.98, "cold":100.00, "pressure":3.37, "temperature":79.94, "time":54631765},
        {"hot":85.47, "cold":100.00, "pressure":3.33, "temperature":79.94, "time":54691899},
        {"hot":85.96, "cold":100.00, "pressure":3.39, "temperature":80.00, "time":54752117},
        {"hot":86.45, "cold":100.00, "pressure":3.39, "temperature":79.94, "time":54812347},
        {"hot":86.94, "cold":100.00, "pressure":3.36, "temperature":79.94, "time":54872403},
        {"hot":87.42, "cold":100.00, "pressure":3.37, "temperature":79.69, "time":54932471},
        {"hot":87.91, "cold":100.00, "pressure":3.40, "temperature":79.81, "time":54992536},
        {"hot":88.40, "cold":100.00, "pressure":3.41, "temperature":79.81, "time":55052694},
        {"hot":88.89, "cold":100.00, "pressure":3.31, "temperature":79.62, "time":55112837},
        {"hot":89.38, "cold":100.00, "pressure":3.34, "temperature":79.44, "time":55172882},
        {"hot":89.87, "cold":100.00, "pressure":3.34, "temperature":79.37, "time":55233102},
        {"hot":90.35, "cold":100.00, "pressure":3.39, "temperature":79.50, "time":55293194},
        {"hot":90.84, "cold":100.00, "pressure":3.39, "temperature":79.44, "time":55353439},
        {"hot":91.33, "cold":100.00, "pressure":3.40, "temperature":79.44, "time":55413598},
        {"hot":91.82, "cold":100.00, "pressure":3.36, "temperature":79.31, "time":55473791},
        {"hot":92.31, "cold":100.00, "pressure":3.44, "temperature":79.31, "time":55533974},
        {"hot":92.80, "cold":100.00, "pressure":3.41, "temperature":79.25, "time":55594021},
        {"hot":93.28, "cold":100.00, "pressure":3.45, "temperature":79.19, "time":55654060},
        {"hot":93.77, "cold":100.00, "pressure":3.41, "temperature":79.12, "time":55714097},
        {"hot":94.26, "cold":100.00, "pressure":3.40, "temperature":79.06, "time":55774172},
        {"hot":94.75, "cold":100.00, "pressure":3.43, "temperature":79.06, "time":55834342},
        {"hot":95.24, "cold":100.00, "pressure":3.45, "temperature":79.12, "time":55894475},
        {"hot":95.73, "cold":100.00, "pressure":3.41, "temperature":79.06, "time":55954517},
        {"hot":96.21, "cold":100.00, "pressure":3.37, "temperature":79.06, "time":56014743},
        {"hot":96.70, "cold":100.00, "pressure":3.37, "temperature":79.06, "time":56074920},
        {"hot":97.19, "cold":100.00, "pressure":3.40, "temperature":79.06, "time":56134946},
        {"hot":97.68, "cold":100.00, "pressure":3.90, "temperature":65.25, "time":56195058},
        {"hot":98.17, "cold":100.00, "pressure":3.48, "temperature":77.69, "time":56255137},
        {"hot":98.66, "cold":100.00, "pressure":3.44, "temperature":78.25, "time":56315324},
        {"hot":99.15, "cold":100.00, "pressure":3.45, "temperature":77.37, "time":56375388},
        {"hot":99.63, "cold":100.00, "pressure":3.43, "temperature":77.00, "time":56435639},
        {"hot":100.00, "cold":100.00, "pressure":3.44, "temperature":76.94, "time":56495838}
    ]
}
----

=== Resource /samples/csv

Values recorded by system scan returned as a csv document, where fields are separated by semicolon.

===== Get /samples/csv response

[source, csv]
----
Hot;Cold;Pressure;Temperature;time
0.000000;100.000000;2.142536;12.312500;44169521
0.488400;100.000000;2.145611;11.375000;44229735
0.976801;100.000000;2.152991;10.500000;44289813
1.465201;100.000000;2.155912;9.812500;44350037
1.953602;100.000000;2.130543;9.312500;44410125
2.442002;100.000000;2.147148;8.875000;44470206
2.930403;100.000000;2.139922;8.500000;44530235
3.418803;100.000000;2.138231;8.187500;44590393
3.907204;100.000000;2.142074;8.125000;44650538
4.395604;100.000000;2.148532;8.000000;44710627
4.884005;100.000000;2.116552;7.937500;44770663
5.372405;100.000000;2.124085;7.875000;44830860
5.860806;100.000000;2.071041;7.812500;44891024
6.349206;100.000000;2.108556;7.750000;44951211
6.837607;100.000000;2.126545;7.750000;45011381
7.326007;100.000000;2.120088;7.687500;45071485
7.814408;100.000000;2.132849;7.687500;45131637
8.302808;100.000000;2.131158;7.687500;45191842
8.791209;100.000000;2.051976;7.687500;45251952
9.279609;100.000000;2.255851;7.625000;45312028
9.768010;100.000000;2.224947;7.625000;45372239
10.256410;100.000000;2.221872;7.687500;45432398
10.744811;100.000000;2.232327;7.687500;45492571
11.233211;100.000000;2.197886;7.687500;45552738
11.721612;100.000000;2.231712;9.250000;45612956
12.210012;100.000000;2.241706;9.687500;45673176
12.698413;100.000000;2.249393;10.625000;45733374
13.186813;100.000000;2.260156;10.812500;45793585
13.675214;100.000000;2.349640;14.437500;45853801
14.163614;100.000000;2.344720;14.687500;45913934
14.652015;100.000000;2.390230;17.500000;45974149
15.140415;100.000000;2.396995;17.750000;46034242
15.628816;100.000000;2.482943;21.937500;46094450
16.117216;100.000000;2.537986;23.875000;46154665
16.605617;100.000000;2.524763;23.937500;46214686
17.094017;100.000000;2.564124;26.000000;46274796
17.582418;100.000000;2.534911;26.500000;46334934
18.070818;100.000000;2.648688;30.375000;46395153
18.559219;100.000000;2.675287;30.750000;46455238
19.047619;100.000000;2.679592;31.125000;46515380
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
----

=== Resource /samples/csv/,

Values recorded by system scan returned as a csv document, where fields are separated by comma.

===== Get /samples/csv/, response

[source, csv]
----
Hot,Cold,Pressure,Temperature,time
0.000000,100.000000,2.142536,12.312500,44169521
0.488400,100.000000,2.145611,11.375000,44229735
0.976801,100.000000,2.152991,10.500000,44289813
1.465201,100.000000,2.155912,9.812500,44350037
1.953602,100.000000,2.130543,9.312500,44410125
2.442002,100.000000,2.147148,8.875000,44470206
2.930403,100.000000,2.139922,8.500000,44530235
3.418803,100.000000,2.138231,8.187500,44590393
3.907204,100.000000,2.142074,8.125000,44650538
4.395604,100.000000,2.148532,8.000000,44710627
4.884005,100.000000,2.116552,7.937500,44770663
5.372405,100.000000,2.124085,7.875000,44830860
5.860806,100.000000,2.071041,7.812500,44891024
6.349206,100.000000,2.108556,7.750000,44951211
6.837607,100.000000,2.126545,7.750000,45011381
7.326007,100.000000,2.120088,7.687500,45071485
7.814408,100.000000,2.132849,7.687500,45131637
8.302808,100.000000,2.131158,7.687500,45191842
8.791209,100.000000,2.051976,7.687500,45251952
9.279609,100.000000,2.255851,7.625000,45312028
9.768010,100.000000,2.224947,7.625000,45372239
10.256410,100.000000,2.221872,7.687500,45432398
10.744811,100.000000,2.232327,7.687500,45492571
11.233211,100.000000,2.197886,7.687500,45552738
11.721612,100.000000,2.231712,9.250000,45612956
12.210012,100.000000,2.241706,9.687500,45673176
12.698413,100.000000,2.249393,10.625000,45733374
13.186813,100.000000,2.260156,10.812500,45793585
13.675214,100.000000,2.349640,14.437500,45853801
14.163614,100.000000,2.344720,14.687500,45913934
14.652015,100.000000,2.390230,17.500000,45974149
15.140415,100.000000,2.396995,17.750000,46034242
15.628816,100.000000,2.482943,21.937500,46094450
16.117216,100.000000,2.537986,23.875000,46154665
16.605617,100.000000,2.524763,23.937500,46214686
17.094017,100.000000,2.564124,26.000000,46274796
17.582418,100.000000,2.534911,26.500000,46334934
18.070818,100.000000,2.648688,30.375000,46395153
18.559219,100.000000,2.675287,30.750000,46455238
19.047619,100.000000,2.679592,31.125000,46515380
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
----

=== Resource /monitors

Monitor is an object which will watch a pin value and tell the device
to log it's value if certain conditions are met.

===== Get /monitors response

Get pin monitors.

So the response object would look something like this.

[source, json]
----
[
    {
        "pin": 51,
        "sampleSum": 0,
        "pinValueLast": 1024,
        "pinValueMargin": 1,
        "sampleCount": 0,
        "sampleTotalCount": 10,
        "nextSampleTime": 21077329,
        "sampleInterval": 1000,
        "minLogInterval": 10000,
        "nextLogTime": 21086329
    },
    {
        "pin": 54,
        "sampleSum": 0,
        "pinValueLast": 408,
        "pinValueMargin": 2,
        "sampleCount": 0,
        "sampleTotalCount": 10,
        "nextSampleTime": 21078329,
        "sampleInterval": 2000,
        "minLogInterval": 100000,
        "nextLogTime": 21176329
    }
]
----

===== Post /monitors request

Add a pin monitor.

[source, json]
----
{
    "minLogInterval": 10000000,
    "pin": 50,
    "pinValueMargin": 10,
    "sampleInterval": 1000,
    "sampleTotalCount": 10
}

----
===== Post /monitors response

[source, json]
----
[
    {
        "pin": 50,
        "sampleSum": 0,
        "pinValueLast": 0,
        "pinValueMargin": 10,
        "sampleCount": 0,
        "sampleTotalCount": 10,
        "nextSampleTime": 73486327,
        "sampleInterval": 1000,
        "minLogInterval": 10000000,
        "nextLogTime": 83485327
    }
]
----

===== Delete /monitors request

Delete a pin monitor.

[source, json]
----
[50]
----
===== Post /monitors response

[source, json]
----
[]
----

=== Resource /whitelist

A Whitelist contains ip addresses of devices allowed to give commands to the device.
To get the current whitelist, you can request the the status object (see: <<Get /status response>> ).

===== Post /whitelist request

Add a ip address to whitelist.

[source, json]
----
{
    "ipaddress":"185.126.62.103"
}
----

===== Post /whitelist response

Current whitelist after post

[source, json]
----
[
    "192.168.1.79",
    "192.168.1.198",
    "185.126.62.103"
]
----

===== Delete /whitelist request

Delete a ip address from whitelist.

[source, json]
----
{
    "ipaddress":"185.126.62.103"
}
----

===== Post /whitelist response

Current whitelist after delete

[source, json]
----
[
    "192.168.1.79",
    "192.168.1.198"
]
----

=== Resource /custom

Commands to fill, stop, drain and change temperature of the hot tub.
 
===== Post /custom request

There are two keys allowed in the request json object, *cmd* and *temperature*.
The *cmd* key is required.  The *temperature* key is optional but can only be used
when *cmd* key value is _fill_ or _update_.

* Available values for the *cmd* key are:
 ** _drain_ - To drain the hot tub
 ** _stop_ - To stop the hot tub
 ** _fill_ - To fill the hot tub
 ** _update_ - To change the desired temperature of the hot tub.
 *** If hot tub is already filling, the desired temperature will change.  In addition, the hot valve flow rate will be changed to adjust the current filling temperature.
 *** If hot tub is already stopped or draining, the desired temperature will change so that
     next time the hot tub starts filling, this temperature will be used.

* Available values for the *temperature* key are:
** A decimal number from 0.00 - 100.00

*Now for some post object examples* 

.Filling the hot tub with the previously set desired temperature +

====== Post object to fill +

[source, json]
----
{
    "cmd": "fill"
}
----

====== Response from successful fill posting +
[source, json]
----
{
    "message":"Filling with currently desired temperature",
    "temperature":37.48
}
----

====== Some more Post objects +

.Filling the hot tub and set desired temperature to 37 +

[source, json]
----
{
    "cmd": "fill",
    "temperature": 37
}
----

.Set desired temperature to 37.76 +

[source, json]
----
{
    "cmd": "update",
    "temperature": 37.756
}
----

.Stopping the hot tub +

[source, json]
----
{
    "cmd": "stop"
}
----

.Draining the hot tub +

[source, json]
----
{
    "cmd": "drain"
}
----

See chapter <<Methods overview>> for an overview.

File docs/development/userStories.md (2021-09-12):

# User stories
This document describes all user stories in more detail.  It should answer what is needs to finish the story.
Each story has a unique identifier and this identifier will be the section name.

## lcd_valve_status
As John, I stand in front of the unit and want know how much the hot and cold valves are open
## lcd_fill
As Kamila, I stand in front of the unit and want to fill the hot tub

## lcd_stop
As Kamila, I stand in front of the unit and want to stop the flow to the hot tub

## lcd_drain
As Kamila, I stand in front of the unit and want to drain the hot tub

## lcd_status_temp
As Kamila, I stand in front of the unit and want to know the water temperature

## lcd_temp
As Kamila, I stand in front of the unit and want to change the water temperature flowing to the hot tub

## lcd_status_flow
As Kamila, I stand in front of the unit and want to know the water flow rate

## lcd_flow_slow
As Kamila, I stand in front of the unit and want to make water flow slowly to the hot tub

## lcd_status_when_full
As Kamila, I stand in front of the unit and want to know when the hot tub will be full

## lcd_status_when_empty
As Kamila, I stand in front of the unit and want to know when the hot tub will be fully drained

## lcd_water_level_predict
As Kamila, I stand in front of the unit and want to know the projected hot tub water level.

## lcd_water_level_current
As Kamila, I stand in front of the unit and want to know the current hot tub water level.  This will be measured using
the [pressure_sensor].

## lcd_pid_change
As John, I stand in front of the unit and want change the PID values 

## lcd_pid_change_auto
As John, I stand in front of the unit and want auto tune the PID values.

## wifi_fill
As Kamila, I want to fill the hot tub via web browser. 

#### How to implement

- Use the custom post request route with these three parameters.
  - __parameters__
    - __cmd__ "flow"
    - __hot__ how much in percentages do you want to open the *hot* valve.
    - __cold__ how much in percentages do you want to open the *cold* valve.

__example post request__ 
__path__: `http://192.168.1.79:6100/custom`

__request object__
```
{
    "cmd":"flow",
    "hot":27.67,
    "cold":100
}
```

- Use the custom post request route with these two parameters.
  - __parameters__
    - __cmd__ "fill"
    - __temperature__ how hot in celsius should the water be, flowing to the hot tub.

__example post request__ 
__path__: `http://192.168.1.79:6100/custom`

__request object__
```
{
    "cmd":"fill",
    "temperature":41.67
}
```

## wifi_stop
As Kamila, I want to stop flow, to and from the hot tub via web browser. 

#### How to implement

- Use the custom post request route with this parameter.
  - __parameters__
    - __cmd__ "stop"

__example post request__ 
__path__: `http://192.168.1.79:6100/custom`

__request object__
```
{
    "cmd":"stop"
}
```

## wifi_drain
As Kamila, I want to drain the hot tub via web browser. 

#### How to implement

- Use the custom post request route with this parameter.
  - __parameters__
    - __cmd__ "drain"

__example post request__ 
__path__: `http://192.168.1.79:6100/custom`

__request object__
```
{
    "cmd":"drain"
}
```

## lcd_status_dim_backlight
As John, I stand in front of the unit and want to change the backlight brightness of the LCD display.

This can be useful to lower the current draw of the display if needed, but this will also allow the device to go dim the
display when it has not been in use for some period of time.

In order for this to be possible a dimmer will need to be added and I would think that the [BC337] Transistor would be
a good candidate.

## lcd_system_scan
As John, I stand in front of the unit and want to make the unit learn how much valves need to open to get desired temperature.
This feature I call "System scan" and it will test and store the results in a file called `system.csv` on a sd card which 
can be later used to search for valve settings for a desired temperature. example file [system.csv](./system.csv)

### Related pages
 * [Readme]
 * [Product requirements]
 * [System requirements]
 * [Product requirements]
 * [User stories]
 * [Hardware]
 * [Releases]

[Readme]: ../../README.md
[Product requirements]: ./productRequirements.md
[System requirements]: ./systemRequirements.md
[User stories]: ./userStories.md
[Hardware]: ./hardware.md
[Releases]: ./releases.md
[pressure_sensor]:./hardware.md#pressure_sensor

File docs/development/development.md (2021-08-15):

# Development

This document contains information about the development decisions of this project.

## System Requirements
What is needed to make this product possible.  What environment? What hardware? The plumbing?
Read about the [System requirements] for more details.

## Product Requirements
What are the [Product requirements] for this project?
What use cases will the project solve?  Who will be using it?
Which [features] will be selected into which [Releases]?

## Upload program

### Via serial
To upload this program firmware using usb you will need to change the file `platformio.ini`.  In that file change the `upload-port` to something like **COM4**, that is if you computer gave the esp32 usb connection the name COM4.  Next, comment out the `upload_protocol` because it does not need to be specified when uploading via serial.  This can be done by adding `;` in front of the line `upload_protocol = espota`.

Example
```
;upload_protocol = espota
upload_port = 192.168.1.231
```

### Via wifi
To upload this program firmware over the air (OTA), you will need to change the file `platformio.ini`. In that file, change the `upload-port` to the **Ip** address of the device.  And change the `upload_protocol` **espota** 

Example
```
upload_protocol = espota
upload_port = 192.168.1.187
```

## Wire frame
The [wireframe] for the project is created in figma, I do not have a professional account so I cannot share it here.

## Tests
See [tests] for information tests for this project.

 ### Related pages
 * [Readme]
 * [Product requirements]
 * [System requirements]
 * [Product requirements]
 * [User stories]
 * [Hardware]
 * [Releases]

[Readme]: ../../README.md
[Product requirements]: ./productRequirements.md
[System requirements]: ./systemRequirements.md
[User stories]: ./userStories.md
[Hardware]: ./hardware.md
[Releases]: ./releases.md
[wireframe]: https://www.figma.com/file/y1b4Cv2xqcNgusC35FyHj3/Water-mixer

[features]: ./productRequirements.md#features
[tests]: ../../test/README.md

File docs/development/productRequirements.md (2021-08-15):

# Product requirements
This Product Requirements Document(PRD) describes the requirements the Water mixer project needs to fulfill.  In this 
document, the Water mixer project and all its components will be referred to as the unit.

## Purpose
The main purpose of this project is to provide a user with an easy way to control water flow to and from a hot tub.  
A user should be able to command the unit to fill a hot tub at a specific temperature.  The user should be able to use 
it to control how fast the water flows to the hot tub and also to drain the hot tub.

To achieve this the unit will need to provide the user with information about it’s status and a way to give it commands.
  The user should be able to get the status and and give commands in two ways:

  * __At premises__ When the user is standing in front of the device he should be able to see it’s status, that is, 
  view the value of any status variable and to be able to give any of the available commands.

  * __Remotely__   When the user is not standing in front of the unit, he should be able to see it’s status, that is, 
  view the value of any status variable and to be able to give any of the available commands.

## Features
To be able to fulfill the purpose of this product the features will need to be described and implemented before release.  
They need to be prioritized and later selected into releases.  High priority features will be released first, 
and other lower priority features will be released later.

### Users
Description of the two main personas this product is intended for.
 
   * __John__ is a 30 years old DIY kind a guy.  John knows a little programming, knows about GitHub and knows 
   JavaScript.  He understands the concept of a API and what a PID controller does, but is no specialist.

   * __Kamila__ is a 11 years old non technical kind a girl.  She knows how to use a web browser on a phone and 
   a computer.

Table column description:
  * __Feature Id__ A short, unique, one word name of a feature
  * __User Story__ As a [persona], I [want to], [so that]
  * __P__ Priority/Importance of the feature. Available values: `H` `N` `L`. Where H=High, N=Normal and L = Low.
  * __R__ Feature is selected into a release numbered something. Read about [Releases].
  * __Notes__ Additional considerations or better explanation of the story.

|  Feature Id | User Story | P | R | Notes |
|:---:|---|---|---|---|
| [lcd_valve_status] | As John, I stand in front of the unit and want know how much the hot and cold valves are open | H | [0.5] | |
| [lcd_fill] | As Kamila, I stand in front of the unit and want to fill the hot tub | H | [0.5] | |
| [lcd_stop] | As Kamila, I stand in front of the unit and want to stop the flow to the hot tub | H | [0.5] | |
| [lcd_drain] | As Kamila, I stand in front of the unit and want to drain the hot tub | H | [0.5] | |
| [lcd_status_temp] | As Kamila, I stand in front of the unit and want to know the water temperature | N | [0.5] | |
| [lcd_temp] | As Kamila, I stand in front of the unit and want to change the water temperature flowing to the hot tub | H | [0.5] | |
| [lcd_pid_change] | As John, I stand in front of the unit and want change the PID values | H | [0.5] | |
| [lcd_system_scan] | As John, I stand in front of the unit and want the system to learn how to get desired temperature | H | [0.5] | |
| [lcd_status_flow] | As Kamila, I stand in front of the unit and want to know the water flow rate | N | [0.7] | |
| [lcd_flow_slow] | As Kamila, I stand in front of the unit and want to make water flow slowly to the hot tub | N | [0.7] | |
| [lcd_pid_change_auto] | As John, I stand in front of the unit and want auto tune the PID values | H | [0.7] | |
| [wifi_fill] | As Kamila, I want to fill the hot tub via web browser. | H | [0.8] | |
| [wifi_stop] | As Kamila, I want to stop flow, to and from the hot tub via web browser. | H | [0.8] | |
| [wifi_drain] | As Kamila, I want to drain  the hot tub via web browser. | H | [0.8] | |
| [lcd_status_when_full] | As Kamila, I stand in front of the unit and want to know when the hot tub will be full | L | [1.0] |  This is after some one has initiated the filling process |
| [lcd_status_when_empty] | As Kamila, I stand in front of the unit and want to know when the hot tub will be fully drained | L | [1.0] |  This is after some one has initiated the draining process |
| [lcd_water_level_predict] | As Kamila, I stand in front of the unit and want to know the projected hot tub water level. | L | [1.0] | |
| [lcd_status_dim_backlight]  | As John, I stand in front of the unit and want to set the backlight brightness of the LCD display. | L | [1.1] | |
| [lcd_water_level_current] | As John, I stand in front of the unit and want to change the backlight brightness of the LCD display. | L | [1.1] | |

 ### Related pages
 * [Readme]
 * [Product requirements]
 * [System requirements]
 * [Product requirements]
 * [User stories]
 * [Hardware]
 * [Releases]

[Readme]: ../../README.md
[Product requirements]: ./productRequirements.md
[System requirements]: ./systemRequirements.md
[User stories]: ./userStories.md
[Hardware]: ./hardware.md
[Releases]: ./releases.md

[Releases]: ./releases.md
[0.5]: ./releases.md#release-05---bare-minimum
[0.6]: ./releases.md#release-06--hardware-installed
[0.7]: ./releases.md#release-07---additional-features
[0.8]: ./releases.md#release-08---remote-access
[0.9]: ./releases.md#release-09---boxed
[1.0]: ./releases.md#release-10
[1.1]: ./releases.md#release-11

[lcd_valve_status]: ./userStories.md#lcd_valve_status
[lcd_fill]: ./userStories.md#lcd_fill
[lcd_stop]: ./userStories.md#lcd_stop
[lcd_drain]: ./userStories.md#lcd_drain           
[lcd_status_temp]: ./userStories.md#lcd_status_temp
[lcd_temp]: ./userStories.md#lcd_temp
[lcd_status_flow]: ./userStories.md#lcd_status_flow
[lcd_flow_slow]: ./userStories.md#lcd_flow_slow
[lcd_status_when_full]: ./userStories.md#lcd_status_when_full
[lcd_status_when_empty]: ./userStories.md#lcd_status_when_empty
[lcd_water_level_predict]: ./userStories.md#lcd_water_level_predict
[lcd_water_level_current]: ./userStories.md#lcd_water_level_current
[lcd_pid_change]: ./userStories.md#lcd_pid_change
[lcd_pid_change_auto]: ./userStories.md#lcd_pid_change_auto
[wifi_fill]: ./userStories.md#wifi_fill
[wifi_stop]: ./userStories.md#wifi_stop
[wifi_drain]: ./userStories.md#wifi_drain 
[lcd_status_dim_backlight]: ./userStories.md#lcd_status_dim_backlight
[lcd_system_scan]: ./userStories.md#lcd_system_scan

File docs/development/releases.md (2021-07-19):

# Releases
The product will not be released all at ones, but rather in stages.  Features will be selected into releases which will 
be released on different dates.  From release 1.0 and onward the product will be considered a usable product, but all 
releases below 1 will be considered experimental.

## Release 0.5 - Bare minimum
This release will have the bare minimum features to work.  The product has been installed and contains a LCD 
touch Display which can be used to give the unit commands.  The unit is connected to [VoffCon] via wifi but no emphasis
is put on the remote part of the unit.  All hardware that should be connected to the unit are not necessarily installed.
  * Date: unknown

## Release 0.6- Hardware installed
All hardware devices are installed and wired to the unit but the software does not necessarily has a interface for them yet.
  * Date: unknown
  * See [Product requirements] for features in release.

## Release 0.7 - Additional features
Additional features have been added to the bare minimum release.
  * Date: unknown

## Release 0.8 - Remote access
The user can get status from the unit and give it commands remotely.  This is done using [VoffCon].
  * Date: unknown

## Release 0.9 - Boxed
The unit has been put into a box and all wires hidden from the user.  The user can only touch the LSD display every
thing else is protected from the user touch.
  * Date: unknown 

## Release 1.0
The unit has been packaged and tested and is ready for the world.
  * Date: unknown

## Release 1.1
The unit has been released but some addons and new features have been maid.
  * Date: unknown

 ### Related pages
 * [Readme]
 * [Product requirements]
 * [System requirements]
 * [Product requirements]
 * [User stories]
 * [Hardware]
 * [Releases]

[Readme]: ../../README.md
[Product requirements]: ./productRequirements.md
[System requirements]: ./systemRequirements.md
[User stories]: ./userStories.md
[Hardware]: ./hardware.md
[Releases]: ./releases.md

[VoffCon]: https://voffcon.com/

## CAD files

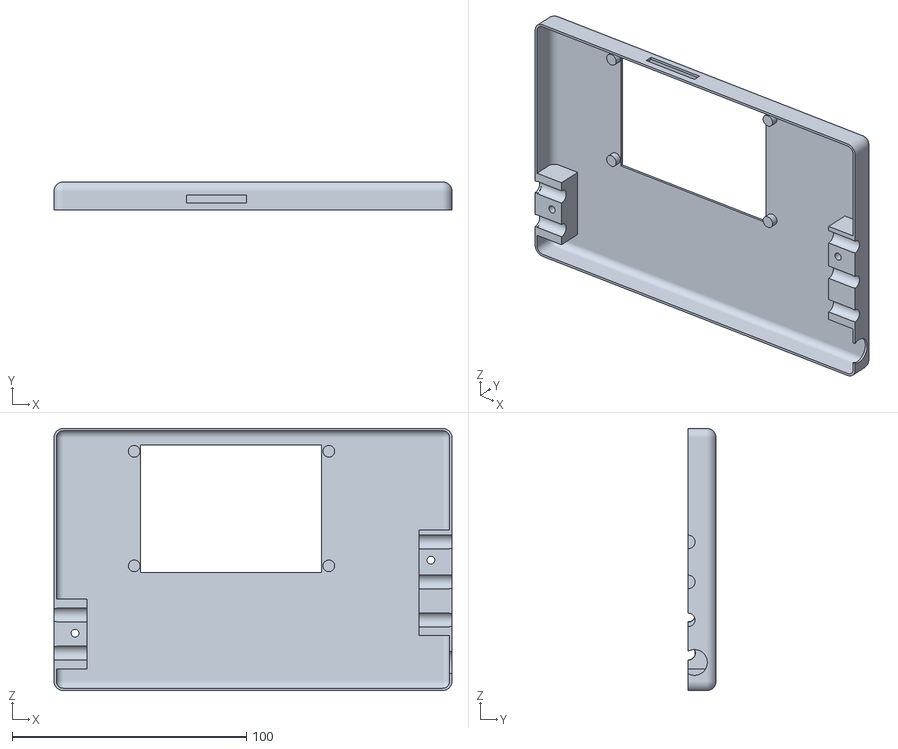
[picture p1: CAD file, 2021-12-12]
hardware/production/box/Box 117x112x40 top.STL
170.0 x 12.0 x 112.0

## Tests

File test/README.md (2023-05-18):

# Tests

These are the standard tests provided by PlatformIO.  These tests run on the
device. More information about [PlatformIO Unit Testing].

__Running the tests__

Assuming the esp32 is connected to the usb on port COM4
```
pio test -e esp32dev --test-port COM6
```

Showing serial print monitor
```
pio test -e esp32dev -v --test-port COM6
```

[PlatformIO Unit Testing]:https://docs.platformio.org/page/plus/unit-testing.html

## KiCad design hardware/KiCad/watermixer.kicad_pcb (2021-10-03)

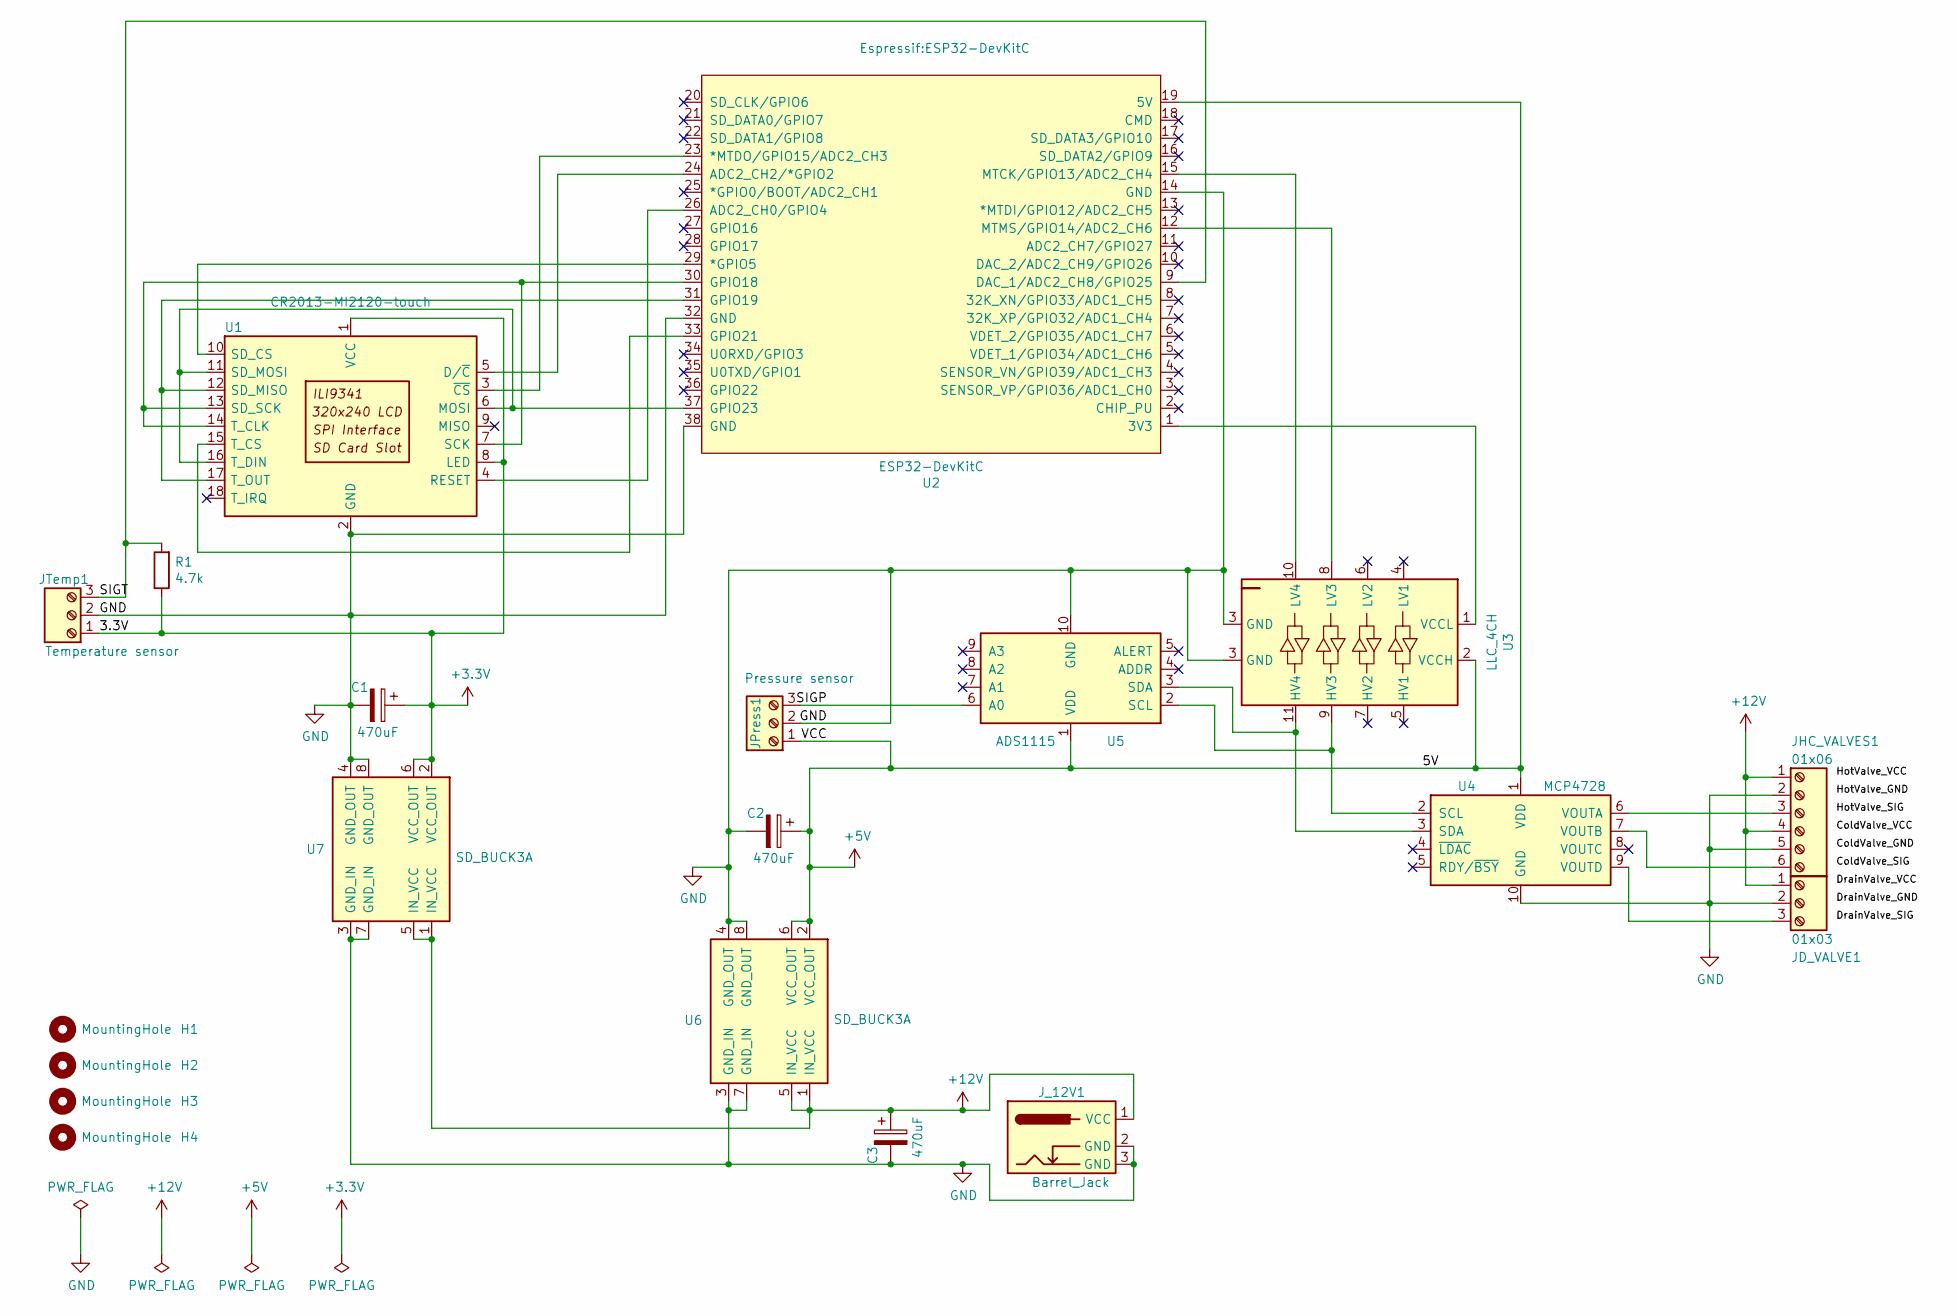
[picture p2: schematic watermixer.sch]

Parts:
C1, C2, C3: 470uF; CP_Radial_Tantal_D8.0mm_P5.00mm
H1, H2, H3, H4: MountingHole; MountingHole_3.2mm_M3
JD_VALVE1: 01x03; Screw_Termianl_01x03
JHC_VALVES1: 01x06; Screw_Termianl_01x06
JPress1: Pressure sensor; Screw_Termianl_01x03
JTemp1: Temperature sensor; Screw_Termianl_01x03
J_12V1: Barrel_Jack
R1: 4.7k; R_Axial_DIN0207_L6.3mm_D2.5mm_P7.62mm_Horizontal
U1: CR2013-MI2120-touch; CR2013-MI2120_touch
U2: ESP32-DevKitC
U3: LLC_4CH
U4: MCP4728; MCP4728_module
U5: ADS1115; ADS1115_module
U6, U7: SD_BUCK3A

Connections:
+3V3: C1.1, JTemp1.1, R1.1, U1.1 (VCC), U1.8 (LED), U7.2 (VCC_OUT), U7.6 (VCC_OUT)
+5V: C2.1, JPress1.1, U2.19 (5V), U3.2 (VCCH), U4.1 (VDD), U5.1 (VDD), U6.2 (VCC_OUT), U6.6 (VCC_OUT)
+12V: C3.1, JD_VALVE1.1, JHC_VALVES1.1, JHC_VALVES1.4, J_12V1.1 (VCC), U6.1 (IN_VCC), U6.5 (IN_VCC), U7.1 (IN_VCC), U7.5 (IN_VCC)
/SIGP: JPress1.3, U5.6 (A0)
/SIGT: JTemp1.3, R1.2, U2.9 (DAC_1/ADC2_CH8/GPIO25)
GND: C1.2, C2.2, C3.2, JD_VALVE1.2, JHC_VALVES1.2, JHC_VALVES1.5, JPress1.2, JTemp1.2, J_12V1.2 (GND), J_12V1.3 (GND), U1.2 (GND), U2.14 (GND), U2.32 (GND), U2.38 (GND), U3.3 (GND), U4.10 (GND), U5.10 (GND), U6.3 (GND_IN), U6.4 (GND_OUT), U6.7 (GND_IN), U6.8 (GND_OUT), U7.3 (GND_IN), U7.4 (GND_OUT), U7.7 (GND_IN), U7.8 (GND_OUT)
unnamed: JD_VALVE1.3, U4.9 (VOUTD)
unnamed: JHC_VALVES1.3, U4.6 (VOUTA)
unnamed: JHC_VALVES1.6, U4.7 (VOUTB)
unnamed: U1.3 (~CS), U2.23 (*MTDO/GPIO15/ADC2_CH3)
unnamed: U1.4 (RESET), U2.26 (ADC2_CH0/GPIO4)
unnamed: U1.5 (D/~C), U2.24 (ADC2_CH2/*GPIO2)
unnamed: U1.10 (SD_CS), U2.29 (*GPIO5)
unnamed: U1.6 (MOSI), U1.11 (SD_MOSI), U1.16 (T_DIN), U2.37 (GPIO23)
unnamed: U1.12 (SD_MISO), U1.17 (T_OUT), U2.31 (GPIO19)
unnamed: U1.7 (SCK), U1.13 (SD_SCK), U1.14 (T_CLK), U2.30 (GPIO18)
unnamed: U1.15 (T_CS), U2.33 (GPIO21)
unnamed: U2.1 (3V3), U3.1 (VCCL)
unnamed: U2.12 (MTMS/GPIO14/ADC2_CH6), U3.8 (LV3)
unnamed: U2.15 (MTCK/GPIO13/ADC2_CH4), U3.10 (LV4)
unnamed: U3.9 (HV3), U4.2 (SCL), U5.2 (SCL)
unnamed: U3.11 (HV4), U4.3 (SDA), U5.3 (SDA)

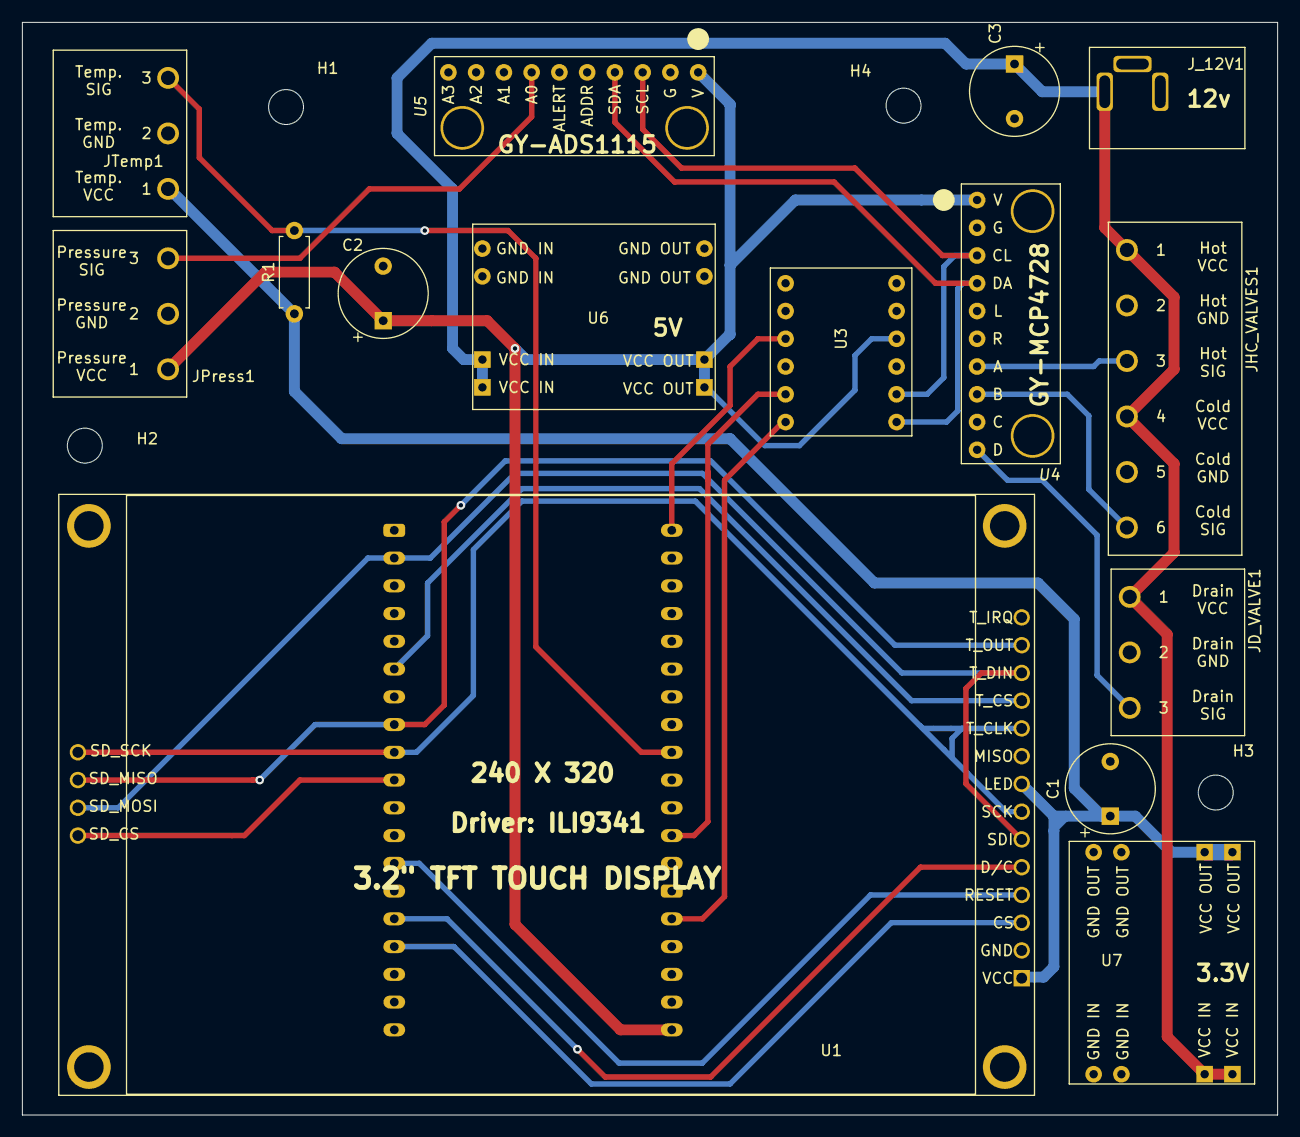
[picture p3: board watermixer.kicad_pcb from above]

Board: 2 copper layers, 114.9 x 100.0 mm, 20 parts (1 on the bottom side), 22 nets.

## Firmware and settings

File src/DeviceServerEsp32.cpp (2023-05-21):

/*
VoffCon is a system for controlling devices and appliances from anywhere.
It consists of two programs.  A "node server" and a "device server".
Copyright (C) 2016  Gudjon Holm Sigurdsson

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
You can contact the author by sending email to gudjonholm@gmail.com or
by regular post to the address Haseyla 27, 260 Reykjanesbar, Iceland.

    Program for Board: ESP32 Dev Module
*/
// #include <FS.h>
// #include <SPI.h>
// #include <SPIFFS.h>

#include <WiFi.h>
#include <HTTPClient.h>

#include "setupMenu.h"
#include "sensors.h"

#include "config.h"
#include "upload-ota.h"
//#include <stddef.h>  //for linked list
/* 
    Board: ESP32 DEV Module
*/

const char* deviceId = "61052c38bc1fdd0526aedf31";
const char *hostName = "watermixer";

// Name of the wifi (accesspoint)network
// example: "guttisWiFi"
const char* ssid = getSsId();
// Wifi password
// example: "mypasswordToTheWifi"
const char* password = getPassword();
// port number which this device will be operating on.
// example: 5100
const int   PORT = 80;
// example: 6100
const int   voffconServerPort = 6100;

IPAddress

// ip address which this device will be operating on.
// Example: "192.168.1.158"     
myIp(192,168,1,185),

//the default gateway which this device will be operating on.
// example: "192.168.1.254"
gateway(192,168,1,254),

// the default gatway on this network.
// On windows goto command
// prompt and type "ipconfig"
// example: "255.255.255.0"
subnet(255,255,255,0),

// example: "192.168.1.127"
voffconServerIp(192,168,1,79);

/*boolean grantAccessToEverybody:
* Set to true if you want to allow all clients where the first 3 numbers
* in a client IP address are the same same as myIp (this server IP address).
.*/
boolean grantAccessToEveryone = false;

boolean grantAccessToAllClientsOnSameSubnet = true;
/*boolean grantAccessToFirstCaller:
* set to true if you want to allow the first client to call the "/setup" method
* to be automaticly granted access.  that is, client IP address will be whitelisted.
.*/

WiFiServer server(PORT);

const int ERROR_NUMBER = -9999;

enum OBJECTTYPE {
    OBJECTTYPE_KEYVALUE_STRING,
    OBJECTTYPE_KEYVALUE_INT,
    OBJECTTYPE_PINS_ARRAY,
    OBJECTTYPE_PIN,
    OBJECTTYPE_PINS,
    OBJECTTYPE_DATE,
    OBJECTTYPE_WHITELIST_ARRAY,
    OBJECTTYPE_STATUS,
    OBJECTTYPE_LOG_PINS,
    OBJECTTYPE_INFORMATION,
    OBJECTTYPE_WARNING,
    OBJECTTYPE_ERROR,
    /*add next type above this line*/
    OBJECTTYPE_COUNT
};

enum JSONTYPEKEY {
    KEYVALUE_STRING,
    KEYVALUE_INT,
    KEYVALUE_DOUBLE
};


/// <summary>
/// A list to store IP addresses
/// </summary>
class IPAddressList : public LinkedList<IPAddress*> {
private:
    void destory();

public:
    bool add(uint8_t first_octet, uint8_t second_octet, uint8_t third_octet, uint8_t fourth_octet);
    bool add(IPAddress address);
    bool add(const char* strIpAddress);
    bool exists(IPAddress address);
    bool exists(String strIpaddress);
    int indexOf(IPAddress address);
    bool isEmpty();
    bool remove(const char *strIpAddress);
    bool remove(IPAddress address);
    String toJson();
    ~IPAddressList();
};

/// <summary>
/// Possible types of a pin are:
/// <para/>PINTYPE_INPUT_ANALOG   : "Read method analogRead shall be used"
/// <para/>PINTYPE_INPUT_DIGITAL  : "Read method digitalRead shall be used"
/// <para/>PINTYPE_OUTPUT_ANALOG  : "Write method analogWrite shall be used"
/// <para/>PINTYPE_OUTPUT_DIGITAL : "Write method digitalWrite shall be used"
/// <para/>PINTYPE_OUTPUT_VIRTUAL : "A pin not connected to hardware, but can store values"
/// </summary>
enum PINTYPE {
    PINTYPE_INPUT_ANALOG,
    PINTYPE_INPUT_DIGITAL,
    PINTYPE_OUTPUT_ANALOG,
    PINTYPE_OUTPUT_DIGITAL,
    PINTYPE_OUTPUT_VIRTUAL 
};

/// <summary>
/// Class for handling GPIO pins
/// Use it to read from or write to a pin
/// </summary>
class GPin {
private:
    int mNumber;
    int mValue;
    PINTYPE mType;
    char *mName;
#ifdef ESP32 
    #define LEDC_TIMER_13_BIT  13
    #define LEDC_BASE_FREQ     8100
    int mChannel;
    void ledcAnalogWrite(uint8_t channel, uint32_t value, uint32_t valueMax = 255);
    void analogWriteEsp32();
#endif
    void init(const char*strPinName, PINTYPE pinType, int pinNumber, int pinValue);
    void set(int number, int value);
    String jsonKeyValue(String key, int value);
    void destroy();
public:
#ifdef ESP32 
    GPin(const char*strPinName, PINTYPE pinType, int pinNumber, int pinValue, uint8_t pinChannel);
#else
    GPin(const char *strPinName, PINTYPE pinType, int pinNumber, int pinValue);
#endif    
    ~GPin();
    void setName(const char*strPinName);
    String getName();
    void setValue(int value);
    int getValue(bool readValueFromHardware = true);
    int getNumber();
    int getType();
    String toJson();
    String toJsonKeyValue();
};

/// <summary>
/// This class stores GPin objects which connect the server to device hardware pins
///<para/>
/// </summary>
class GPins {
private:
    int mLength = 0;
#ifdef ESP32 
    int mChannelCount = 0;
#endif
    GPin *mPins[30];//todo: I make this dynamic, instead of a fixed size
    int indexOf(int pinNumber);

public:
    int addPin(const char *strPinName, PINTYPE pinType, int pinNumber, int pinValue);
    boolean setValue(int pinNumber, int newValue);
    boolean exists(int pinNumber);
    GPin *get(int pinNumber);
    int getValue(int pinNumber);
    int count();
    String toJson();
    String JsonPinout();
    GPins();
};

/// <summary>
/// Used to store time.
/// Depended on which constuctor is used, values can be eather a "date and time" or a "counter" up to 49 days. 
/// </summary>
class GTime {
    ///////////////////////////////////////////////////////////
private:
    int mYear = 0;
    int mMonth = 0;
    int mDay = 0;
    int mHours = 0;
    int mMinutes = 0;
    int mSeconds = 0;
public:
    GTime() { }
    GTime(const GTime& gTime);
    GTime(unsigned long milliSeconds);
    void setTime(unsigned long milliSeconds);
    boolean setTime(String strTime);

   
    int strToMonth(String month);
    static int toNumber(String str);
    String toString();
   
    String toStreng();
   
    String toJson();
    int getYear(); 
    int getMonth();
    int getDay();
    int getHours();
    int getMinutes();
    int getSeconds();
};

/// <summary>
/// Used to store only Number and value of a pin
/// </summary>
struct PinValue
{
    int pinNumber;
    int pinValue;
};

class GUrl {
private:
    int mLength = 0;
public:
    GUrl() { }
    int toNumber(String str);
    static String jsonKeyValue(String key, String value);
    static String jsonKeyValue(String key, int value);
    static String jsonObjectType(unsigned int uiType);
    static String makeStatusResponceJson(String jsonPins, String jsonWhitelist, String jsonDate, String macAddress, String deviceId, String hostName, String deviceIpAddress, int port, String jsonMixer);
    
    static String makePostLogPinsJson(String deviceId, String jsonPins);
    static String makeHttpStatusCodeString(unsigned int uiStatusCode);
    static String jsonRoot(unsigned int uiType, String key, String value);
};

/// <summary>
/// The errornumber to return when a numberfunction fails;
/// Like: toInt(), toFloat(), toLong(), toULong()
/// </summary>
#define JSONDATA_ERRORNUMBER 999999999

//See informanation on JSON on https://www.json.org (nice pictures)
//See more info here : https://www.crockford.com/mckeeman.html
//todo: Hexadecimal digits can be represented as u and then 4 hexadecimal digits. (\u hex hex hex hex)
//      hex can be ('0'..'9' or 'A'..'F' or 'a'..'f')
//todo: Exponent numbers see second answser: https://stackoverflow.com/questions/19554972/json-standard-floating-point-numbers
//      example1: 1e-005 example2: 2.99792458e8   Exponent can be ('E' sign digits) or ('e' sign digits)
/// <summary>
/// Enumeration for which type of json object the json data is.
/// </summary>
enum JSONTYPE {
    JSONTYPE_INVALID,
    JSONTYPE_ARRAY,
    JSONTYPE_OBJECT,
    JSONTYPE_KEY_VALUE,
    JSONTYPE_STRING,
    JSONTYPE_ULONG,
    JSONTYPE_LONG,
    JSONTYPE_FLOAT,
    JSONTYPE_BOOL,
    JSONTYPE_NULL,
};

/// <summary>
/// Class for representing elements and objects in a json object.
/// You can use it to browse and get values and add and remove objects from a json.
/// </summary>
/// <example>
/// Example hello World:
/// @code{.xml}
///     // Create an json object with one key named "hello"
///     // and one value which is the string "world"
///     JsonData js("{\"hello\":\"world\"}");
/// @endcode
/// </example>
class JsonData
{

private:

    String       mValue;
    JSONTYPE     mType;
    JSONTYPE     mValueType;
    JsonData    *mFirstChild{},
                *mNext{},
                *mParent{};

    JsonData(JSONTYPE type, JsonData* parent);
    JsonData(String jsonString, JsonData* parent);
    JsonData(String value, JSONTYPE type, JSONTYPE valueType, JsonData* parent);

    static bool      isClosingToken(char c);
    static char      getClosingToken(char openingToken);
    static int       getIndexOfClosingToken(String* string, bool ignoreStrings);
    static bool      isDigit(char c);
    static bool      removeLast(JsonData* pNode);
    static bool      destroyIncludingChildren(JsonData* pNode);
    static JSONTYPE  getValueTypeFromChar(char firstCharInValue);
    static JSONTYPE  getType(String strValue);
    static JsonData *getLastChild(JsonData* parent);
    static JsonData *getLastNode(JsonData* previous);
    static JsonData *getPointingNode(JsonData* findMe);
    static JsonData *findPointingNode(JsonData* startFrom, JsonData* findMe);
    static JsonData *getRootNode(JsonData* current);
    void             init(JSONTYPE type, JSONTYPE valueType, JsonData* parent);
    void             parse(const String jsonString, JsonData* parent);
    JsonData        *setRootInvalid();
    String           valueToString();
    JsonData        *array(String* elements, JsonData* parent, bool canBeMoreThanOne);
    JsonData        *object(String* members, JsonData* parent);
    JsonData        *elements(String* values, JsonData* parent);
    bool             getPairIndexes(String* pairs, bool& thereIsAnotherPair,
                                    int    &keyIndexOfFirstChar, int& keyLength,
                                    int    &valueIndexOfFirstChar, int& valueLength,
                                    int    &pairLength);
    JsonData        *members(String* pairs, JsonData* parent);
    JsonData        *pair(String* keyValues, JsonData* parent);
    static bool      validateValue(const JSONTYPE jsonvaluetype, String string);
    JsonData       *value(String* valuesString, JsonData* parent);
    static String   jsonTypeString(JSONTYPE type);
    String          toTree(JsonData* current, int level);
    static bool     isWhitespace(const char c);
public:
    JsonData(const char* jsonString);
    ~JsonData();
    String        toString();
    String        toTree();
    static String trim(String jsonStringToTrim);
    bool          isValid() const;
    /// <summary>
    /// Checks if the current object has any child objects
    /// </summary>
    /// <returns>
    /// true if this object has one ore more child object(s).  Otherwize false
    /// </returns>
    bool          hasChildren() { return this->mFirstChild != NULL; };
    JsonData     *getChildAt(unsigned int index);
    JsonData     *getChild(String value);
    JsonData     *getNext();
    const String  getValue();
    String        getValueAsString();
    float         getValueAsFloat();
    unsigned long getValueAsULong();
    long          getValueAsLong();
    int           getValueAsInt();
    JSONTYPE      getType()      const { return mType; }
    JSONTYPE      getValueType() const { return mValueType; }
};

/// <summary>
/// A class for parsing json strings
/// </summary>
/// <example>
/// Example on how to create a json object from a string:
/// @code{.xml}
/// Json json("{\"hello\":\"world\",\"array\":[1,2,-4,-5.22,\"string in a array\"]}");
/// @endcode
/// </example>
class Json
{
    JsonData *mData;
public:
    Json(const char *jsonString);
    ~Json();
    String toString() const;
	String toTree() const;
    static String trim(String jsonStringToTrim);
    bool isValid() const;
    /// <summary>
    /// Use this function access the root JsonData object
    /// </summary>
    /// <returns>
    /// The root JsonData object.
    /// If the object is invalid NULL is returned.
    /// </returns>
    JsonData *getRootObject() { return mData == NULL || !mData->isValid()? NULL: mData; };
};
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
void loop() {
    if (millis() > _tellServerToSaveLogTimer)
        tellServerToSaveLog(false);
    ArduinoOTA.handle();
    if (checkAndUpdateSensors())
        updateDeviceVirtualPinValues();
    reconnectIfDisconnected();
    //Serial.printf("%.3f°  %.3f PSI\n", currentTemperature, currentPressure);
    menu.update();
    drawLinkedButtonsAndLabels();
    
    //timerTwoSeconds();
    if (monitors.isAnyPinWatchDo()) {
        // One item did trigger so you could log
        tellServerToSaveLog(false);
        monitors.resetAllChecks();
    }
    
    // listen for incoming clients
    WiFiClient client = server.available();
    if (client) {
        Serial.println("New client");
        memset(linebuf, 0, sizeof(linebuf));
        charcount = 0;
        // an http request ends with a blank line
        boolean currentLineIsBlank = true;
        while (client.connected()) {

            if (client.available()) {
                char c = client.read();
                Serial.write(c);
                //read char by char HTTP request
                linebuf[charcount] = c;
                if (charcount < sizeof(linebuf) - 1) charcount++;
                // if you've gotten to the end of the line (received a newline
                // character) and the line is blank, the http request has ended,
                // so you can send a reply
                if (c == '\n' && currentLineIsBlank) {

                    if (client.available() > 0) {
                        // we still got data to read, there is something after the header
                        // that is there was data after the header
                        if ((method == METHOD_POST || method == METHOD_DELETE) && contentLength > 0) {
                            //Here should contentLength == client.available()
                            for (int ix = 0; ix < contentLength; ix++) {
                                char ch = client.read();
                                linebuf[ix] = ch;
                            }
                            Serial.println(linebuf);
                            //if ( command == COMMANDS_POST_PINS && lib.extractAndSetPinsAndValues(linebuf, &pinnar)) {
                            if (command == COMMANDS_POST_PINS) {
                                setPinValues(linebuf, &devicePins);
                                handlePins(&client);
                            }
                            else if (command == COMMANDS_POST_WHITELIST) {
                                if (isAuthorized(&client))
                                    whiteList.add(getKeyValueFromJsonAsString(linebuf, "ipaddress").c_str());
                                client.println(makeJsonResponseString(200, whiteList.toJson()));
                            }
                            else if (command == COMMANDS_DELETE_WHITELIST) {
                                if (isAuthorized(&client))
                                    whiteList.remove(getKeyValueFromJsonAsString(linebuf, "ipaddress").c_str());
                                client.println(makeJsonResponseString(200, whiteList.toJson()));
                            }

                        } // if (method == METHOD_POST && contentLength > 0) 
                    }
                    if (command == COMMANDS_NOTSET)
                        handleNotFound(&client);// send a standard http response header
                    break;
                }
                if (c == '\n') {
                    // you're starting a new line
                    currentLineIsBlank = true;
                    if (strstr(linebuf, "GET /started") > 0) {
                        method == METHOD_GET;

                        Serial.println(" /started");
                        String str = "{\"date\":";
                        String itemJson = startTime.toJson();
                        str += itemJson;
                        str += "}";
                        Serial.println("timi");
                        Serial.println(str);
                        client.println(makeJsonResponseString(200, str));
                        break;
                    }

                    else if (strstr(linebuf, "GET /pinout") > 0) {
                        method = METHODS::METHOD_GET;
                        handleGetPinout(&client);
                        break;
                    }
                    else if (strstr(linebuf, "GET /pins") > 0) {
                        handlePins(&client);
                        break;
                    }
                    else if (strstr(linebuf, "GET /status") > 0) {

                        handleStatus(&client);
                        break;
                    }
                    else if (strstr(linebuf, "GET /samples/csv/,") > 0) {
                        handleSamplesCSV(&client, ',');
                        break;
                    }
                    else if (strstr(linebuf, "GET /samples/csv") > 0) {
                        handleSamplesCSV(&client);
                        break;
                    }
                    else if (strstr(linebuf, "GET /samples") > 0 ) {
                        handleSamplesJson(&client);
                        break;
                    }
                    else if (strstr(linebuf, "GET /monitors") > 0) {
                        handleMonitors(&client, METHODS::METHOD_GET);
                        break;
                    }
                    else if (strstr(linebuf, "POST /monitors") > 0) {
                        handleMonitors(&client, METHODS::METHOD_POST);
                        break;
                    }
                    else if (strstr(linebuf, "DELETE /monitors") > 0) {
                        handleMonitors(&client, METHODS::METHOD_DELETE);
                        break;
                    }
                    else if (strstr(linebuf, "GET /custom") > 0) {
                        handleCustom(&client, METHODS::METHOD_GET, linebuf);
                        break;
                    }
                    else if (strstr(linebuf, "POST /custom") > 0) {
                        handleCustom(&client, METHODS::METHOD_POST, linebuf);
                        break;
                    }
                    else if (strstr(linebuf, "DELETE /custom") > 0) {
                        handleCustom(&client, METHODS::METHOD_DELETE, linebuf);
                        break;
                    }
                    else if (strstr(linebuf, "POST /pins") > 0) {
                        method = METHODS::METHOD_POST;
                        command = COMMANDS::COMMANDS_POST_PINS;
                    }
                    else if (strstr(linebuf, "POST /whitelist") > 0) {
                        method = METHODS::METHOD_POST;
                        command = COMMANDS::COMMANDS_POST_WHITELIST;
                    }
                    else if (strstr(linebuf, "DELETE /whitelist") > 0) {
                        method = METHODS::METHOD_DELETE;
                        command = COMMANDS::COMMANDS_DELETE_WHITELIST;
                    }
                    else if (strstr(linebuf, "Content-Length: ") > 0) {
                        String strTemp = String(strstr(linebuf, "Content-Length: ") + 16);
                        strTemp.replace("\r", ""); strTemp.replace("\n", "");
                        contentLength = GTime::toNumber(strTemp);
                    }

                    // you're starting a new line
                    currentLineIsBlank = true;
                    memset(linebuf, 0, sizeof(linebuf));
                    charcount = 0;
                }
                else if (c != '\r') {
                    // you've gotten a character on the current line
                    currentLineIsBlank = false;
                }
            }//if (client.available())
        }//while (client.connected()) 
        
        // give the web browser time to receive the data
        delay(1);
        // close the connection:
        method = METHODS::METHOD_NOTSET;
        command = COMMANDS::COMMANDS_NOTSET;
        client.stop();
        contentLength = 0;
        Serial.println("client disconnected");
    }
}
///////////////////////////////////// IMPLEMENTATION OF ALL CLASSES  /////////////////////////////////////

#ifndef CODE_BLOCK_IPAddressList

/// <summary>
/// The deconstructor, which cleans up when the list is no longer needed.
/// </summary>
IPAddressList::~IPAddressList() { 
    destory();
}
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

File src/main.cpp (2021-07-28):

/*
    serial_valves.cpp
 Gets values (0 - 1) from serial and writes it with PWM to pins 32 and 33.

 Type to the serial character c or h followed by a real number to 
 change the opining of one of the two valves.
*/

#include <Arduino.h>
#include "valve.h"

#include "globals.h"

const int pinHot = 32;
const int pinCold = 33;
#define FULL_DUTY 255
#define MAX_DUTY 190
#define CHANNEL_1 1
#define CHANNEL_2 2

Valve hot(pinHot, CHANNEL_1, FULL_DUTY, MAX_DUTY, 0.0, "Hot valve");
Valve cold(pinCold, CHANNEL_2, FULL_DUTY, MAX_DUTY, 0.0, "Cold valve");

void setup()
{
    Serial.begin(115200);
    values.pid.input = 23;
    

    hot.serialPrintInfo();
    cold.serialPrintInfo();
    Serial.println("Type character c or h followed by a real number to change the opining of one of the two valves.\n");
    Serial.println("Where values:");
    Serial.println("   h0 : Fully closes the hot valve.");
    Serial.println(" c0.5 : Opens the cold valve half way.");
    Serial.println("   c1 : Fully opens the cold valve.");
}

String strInput = "";
char c;

void loop()
{
    while (Serial.available() > 0)
    {
        c = Serial.read();
        if (c == '\n')
        {
            Serial.print("Got string : \"");
            strInput.toUpperCase();
            Serial.print(strInput + "\" ");
            if (strInput.length() < 2)
            {
                Serial.println(" Invalid input");
            }
            else
            {
                if (strInput.startsWith("H"))
                {
                    double value = strInput.substring(1).toFloat();
                    Serial.print(String(" New value: ") + String(value) + " -> ");
                    hot.setFlow(value);
                }
                else if (strInput.startsWith("C"))
                {
                    double value = strInput.substring(1).toFloat();
                    Serial.print(String(" New value: ") + String(value) + " -> ");
                    cold.setFlow(value);
                }
                else
                {
                    Serial.println(" Invalid input");
                }
            }
            strInput = "";
        }
        else
        {
            strInput += c;
        }
    }
    delay(200);
}

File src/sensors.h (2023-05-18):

#ifndef SENSORS_H
#define SENSORS_H

#include "globals.h"

unsigned long timerReadTemperature;

void setupSensorTemperature() {
    Serial.println("Setting up sensors");
    timerReadTemperature = 0;
    sensors.begin();
    sensors.setWaitForConversion(false);
    sensors.requestTemperatures(); 
    sensors.setResolution(9);
}

void setupSensorAdc() {
  // Getting single-ended readings from AIN0..3
  // ADC Range: +/- 6.144V (1 bit = 3mV/ADS1015, 0.1875mV/ADS1115)
  // Try to initialize ADC!
  Serial.println("Setting up the Analog to Digital Converter ADS1115");
  values.pressureSensorIsActive=ads.begin();
  if (!values.pressureSensorIsActive) {
    Serial.println("Error: Failed to initialize ADS. (For pressures sensing)");
    // while (1);
  }
}


/**
 * @brief Get the temperature
 * 
 * @param value to store the temperature
 * @return true when read a new value and stored it.
 * @return false when no new value was read and therefore the value is unchanged.
 */
bool readTemperature(double *value) {
  
  unsigned long now = millis();
  if (now >= timerReadTemperature) {
    double readTemperature = sensors.getTempCByIndex(0); //this takes about 27 milliseconds 3 more ms are added when setWaitForConversion true
    bool readWithSuccess = readTemperature != -127;
    if (readWithSuccess)
      *value = readTemperature;
    sensors.requestTemperatures();//this takes about 3 milliseconds when setWaitForConversion is false on otherwise 597 milliseconds
    // default resolution is 9, and formula for needed delay = 750/ (1 << (12-resolution)) -> and there for 750/ (1 << 3) is equal to 93 ms
    timerReadTemperature = millis() + (750/ (1 << (12-sensors.getResolution()))); //read temperature tent times per second.
    return readWithSuccess;
}
  return false;

}

/**
 * @brief Get the pressure
 * 
 * @return double number in BAR
 */
double readPressure() {
  
  // 5 psi should give full power that is 4096
  // todo: bought a new sensor which is 60 psi
  // todo: this scale should be in bars not volts when the new sensor arrives
  int16_t adc0 = ads.readADC_SingleEnded(0);
  
  //float volts0 = ads.computeVolts(adc0);
  
  //if volts is 5 then PSI = 60 PSI (pounds per square inch) and BAR = 4.13685438
  //The 5 PSI sensor sends 5.05 volts when filling the hot tub so I'm setting that as the max value
  //The 5 PSI sensor sends 26906 value when filling the hot tub so I'm setting that as the max value
  // so 26906 / 4.13685438 = 6503.975613 which is the ratio between the value and BAR units 

  double ret = adc0 / (double)6503.975613;
  
  return ret;
  
}

/**
 * @brief Checks if it's time to read a new value from sensors and updates values if it is time
 * 
 */
bool checkAndUpdateSensors() {
   
  if (values.pressureSensorIsActive) {
    currentPressure = readPressure();
    water.setCurrentPressure(currentPressure);
  }

  readTemperature(&currentTemperature);
  water.setCurrentTemperature(currentTemperature);
  //todo: return false if both Pressure sensor and Temperature are offline

  return true;
}

#endif

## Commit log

2021-06-27 pretting readme wiring
2021-06-27 adding PWM to voltatem test program
2021-06-27 fix pwm link
2021-06-29 valve is functional
2021-06-29 adding serial.print to serial_valve.cpp example
2021-06-29 temperature sensor, adding DallasTemperature and OneWire
2021-06-30 started on watermixer, and fixed double macthing in tests
    [main.cpp, test_main.cpp]
2021-07-03 adding flowmocker
2021-07-03 Fixing setChangeStepInterval in FlowMocker
    [test_main.cpp]
2021-07-14 adding valve status to user story
2021-07-15 adding story "change the PID values"
2021-07-16 Adding pressure sensor example sketch
2021-07-20 moving pressure sensor reading down to 1.1
2021-08-03 can manually control valves hot, cold, drain
2021-08-04 Redrawed the schematic showing current pins and connections
2021-08-04 removing extra spaces from schematic
2021-08-04 shorting the schematic
2021-08-04 Merging the two schematics
2021-08-04 schematic small fix
2021-08-05 Making temperature reading non-blocking and pressure reading return average of 30 samples
2021-08-06 can scan system and fill from desired temperature
2021-08-07 adding upload program wirelessly
    [system.csv]
2021-08-15 adding fill, drain stop and flow commands to /custom route
2021-08-15 can fill remotly without specifyig temperature
2021-09-11 replacing ledcAnalogWrite with setChannelValue from Adafruit_MCP4728 library and removing unnessacery tests
2021-09-11 Removing PWM to Voltage converter and adding DAC to documentation
2021-09-12 BC337 is not needed, we can use pwm from the eps32 pin
2021-09-14 Started designing PCB in KiCad
    [watermixer.kicad_pcb, watermixer.sch]
2021-09-14 All Compoents created and added to Schematic
    [watermixer.sch]
2021-09-15 Done connecting all parts on the schema
    [watermixer.sch]
2021-09-15 got a error free schematic
    [watermixer.sch]
2021-09-15 power fixes before running starting PCB editor
    [watermixer.sch]
2021-09-15 Pcb parts placed, but no traces yet
    [watermixer.sch]
2021-09-16 Connected all on PCB except GND
    [watermixer.kicad_pcb, watermixer.sch]
2021-09-16 before grounding
    [watermixer.kicad_pcb]
2021-09-16 added GND fill zones on top and bottom layers
    [watermixer.kicad_pcb]
2021-09-16 Exported the production files
    [watermixer-B_Cu.gbr, watermixer-B_Mask.gbr, watermixer-B_Paste.gbr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]
2021-10-02 starting to add an ADC
    [watermixer-B_Cu.gbr, watermixer-B_Mask.gbr, watermixer-B_Paste.gbr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]
2021-10-02 added ADS1115 to pcb and ordered 5 pcbs with current production
    [watermixer-B_CrtYd.gbr, watermixer-B_Cu.gbr, watermixer-B_Fab.gbr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]
2021-10-03 Adding SDS1115 to Schematic in README.md
2021-10-03 reading pressure value from ADS1115
2021-10-16 adding mesurements for 3d printing
2021-12-12 Adding hostname= "WaterMixer"
    [Box 117x112x40 top.STL]
2023-05-20 adding update command to voffcon and device and calculating waterlevel
2023-05-21 adding GET /samples and /samples/csv
2023-05-21 adding api metods documentation and a get methods to download samples /samples

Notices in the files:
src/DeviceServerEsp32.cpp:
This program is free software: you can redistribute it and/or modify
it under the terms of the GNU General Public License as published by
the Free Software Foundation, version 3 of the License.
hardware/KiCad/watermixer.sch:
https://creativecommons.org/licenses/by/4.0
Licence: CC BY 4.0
